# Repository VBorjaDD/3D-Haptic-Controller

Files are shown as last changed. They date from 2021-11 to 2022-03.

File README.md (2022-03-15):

# 3D Haptic Controller
Based on the semester project outcome of Louis Jouret (September 2021- January 2022). Supervisor Victor Borja
Detailed information can be found in [FlyingCelluloReport.pdf](/FlyingCelluloReport.pdf)

## Abstract
This project aims to study the feasibility of haptic feedback in a 3D space. There is an increasing demand for such solutions, mainly in rehabilitation since they remove the need for a daily appointment with a therapist and enable the gamification of rehabilitation.
Some solutions already exist but remain very expensive since they are based on 3-axis arms. Nowadays, a lot of progress in the field of aerial robotics has been done and it is time to consider using the principles of flying drones to take over this task.

## Chasis design and flow simulation
The first approach to the solution consist on a graspable device which includes 4 propellers. The device should account for the user safety as well as for the air flow of the chasis. The proposed solution flow simulation is presented bellow.
Flow

## Trajectory control
To provide an adecuate haptic feedback the device needs to be controlled accuratelly, both to provide a good trajectory as well as "Reject disturbances", which in this case would consist on fighthing the weight of the hand, or providing a resistance against the movement as an exercise.

Control

## State of the protype and stabilization test
Bellow it can be found videos of the last stabilizing test:

https://user-images.githubusercontent.com/30259634/156215392-c507a673-42e5-492a-a674-068f0fa65a87.mp4

https://user-images.githubusercontent.com/30259634/156215643-9cf9c3b2-c321-48e0-aff9-d65be72161e4.mp4

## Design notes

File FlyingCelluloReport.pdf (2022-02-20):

## Flying cellulo for rehabilitation

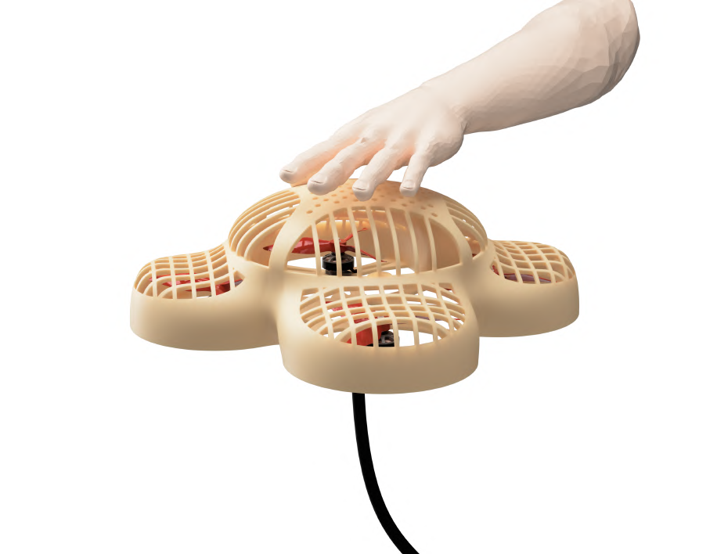
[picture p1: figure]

Louis JOURET - 269882

Professor: Pierre Dillenbourg Advisor: Victor Borja

December 2021

Flying Cellulo for rehabilitation

## Contents

1 Introduction | 1
2 Existing solutions | 1
3 Design | 3
4 Dynamics | 11
5 Control | 12
6 Testing | 17
7 Conclusion | 19

## 1 Introduction

This project aims to study the feasibility of haptic feedback in a 3D space. There is an increasing demand for such solutions, mainly in rehabilitation since they remove the need for a daily appointment with a therapist and enable the gamification of rehabilitation. Some solutions already exist but remain very expensive since they are based on 3-axis arms. Nowadays, a lot of progress in the field of aerial robotics has been done and it is time to consider using the principles of flying drones to take over this task.
The second goal of the project is to propose a proof of concept. Thus a first design will be drawn which will serve us to analyze the technical challenges that have to be overcome to make it a viable solution for rehabilitation. Among these challenges, we count the diculty to draw a graspable drone that remains completely safe and the writing of a control algorithm that is fast enough to create a user-friendly experience.
This work will, first of all, see what has already been done in the field of machine-assisted rehabilitation. Second of all, we will design a first concept that fulfills all the mechanical requirements. Once the design has been done, the dynamics of the model are studied to finally write two dierent control algorithms. The technical work ends with tests of the first material purchased and the first test of haptic feedback. Finally, we will discuss if a flying rehabilitation drone is a feasible solution.
Below is the Gantt chart initially defined at the start of the semester:

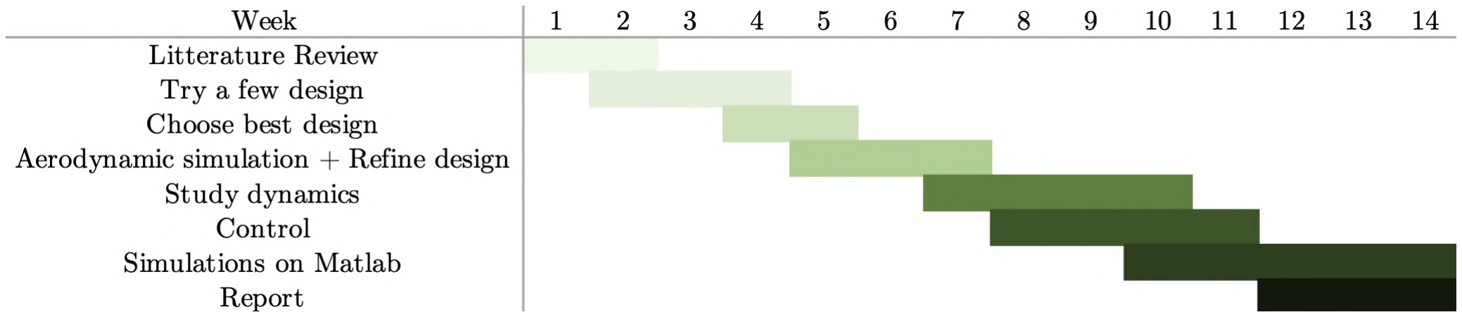
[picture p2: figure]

## 2 Existing solutions

There already exist solutions that are designed for rehabilitation. They are mainly based on a robotic arm that creates haptic feedback to the patient’s hand. One of the most famous products is MIT-Manus. The patient puts his elbow in a support which is held by a robotic arm. The patient then performs dierent movements which are corresponding to divers exercises shown on the screen attached to the robotic arm.

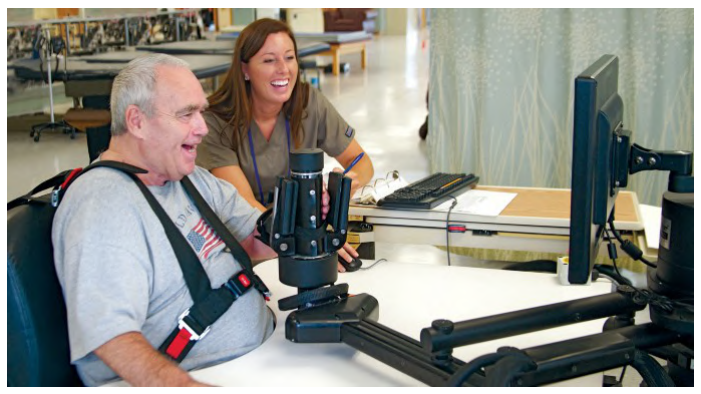
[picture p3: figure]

Figure 1: MIT-Manus [1], Credit: H. I. Krebs, Newman Lab, MIT

Hocoma, which is one of the world leader in advanced technologies for movement rehabilitation, has a complete range of 3 products called Armeo®, designed for the rehabilitation of the arm depending on the severity of the handicap.

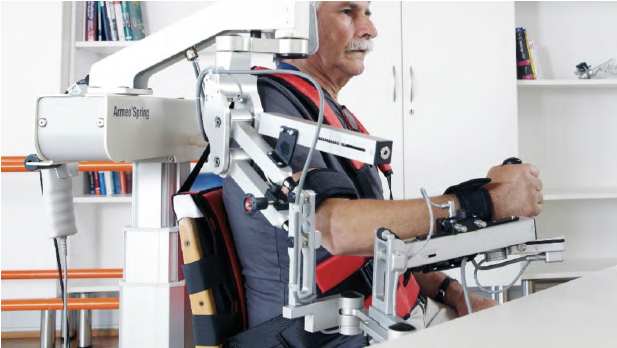
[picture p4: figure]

(a) Armeo®Power | (b) Armeo®Spring

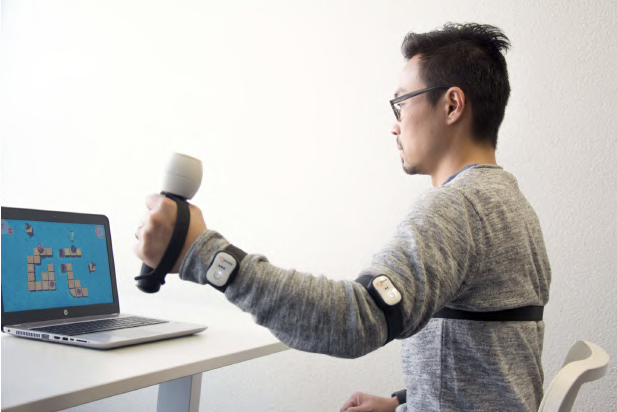
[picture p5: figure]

(c) Armeo®Senso
Armeo®Power [2] is the most powerful solution and can assist and guide the patient’s hand in its movements. Armeo®Spring [3] is a lighter product designed to support the arm’s weight and is thus less powerful. These products come with their monitor on which the patient follows instructions. Armeo®Senso [4]is the lightest product designed for people that can already support the weight of their own arm.
So if a patient needs a product that can create haptic feedback and support the arms weight, the only solutions available are very expensive and impossible to bring home. Thus a flying Cellulo which is capable of supporting the patient’s arm and giving haptic feedback would add value to the market if it can achieve these goals.

## 3 Design

First of all, the power of the Cellulo has to be determined. Since the product needs to assist the patient’s hand and that it should also be able to create resistance, the weight of an adult’s hand is taken as a reference load. Thus the drone should be able to lift the hand without the patient’s help. A simple weighting of 3 dierent hands in dierent positions, gives a maximum weight of 1.5 kg.
Secondly, the fingers have to be protected from the blades. The hand must either be far away from any moving part or the latter have to be covered by a protective grid.
The project is also considering controlling the final product with common video game consoles such as Wii, PlayStation or XBox. Therefore it is necessary to work with a communication protocol that is supported by these platforms. Bluetooth happens to be compatible with the three of them.
Finally, the patient must be able to use the product over a whole workout session, which is not possible with the current battery technology. Hence, the drone has to be supplied with power from the ground. This is not a limiting factor for the user-friendliness of the product since it does not need to fly far away from the ground station.
Thus, the basic requirements that have to be respected whatever the design of the product, are the following:
1. thrust of up to 1.5 kg + own weight
2. safety from the blades
3. Bluetooth as communication protocol
4. no battery on-board

### 3.1 Feasible architectures

There are a lot of very dierent architectures possible to make a drone fly. However, each comes with its perks and drawbacks. Let’s take a closer look at the ones that would be capable of achieving the desired goal:

### 3.1.1 Quadcopter

Figure 3: motor layout of a quadcopter

The quadcopter uses 4 motors which are equidistant to the drone’s center. It is the most seen and popular architecture due to its stability and controllability. Due to its 4 motors, it is the most powerful of the following solutions. However, this comes with high power consumption. But since we are supplied from the ground and are thus not limited by power consumption. The biggest disadvantage of the quadcopter is its footprint. Due to the four propeller, it is not possible to create a compact solution.

### 3.1.2 Tricopter

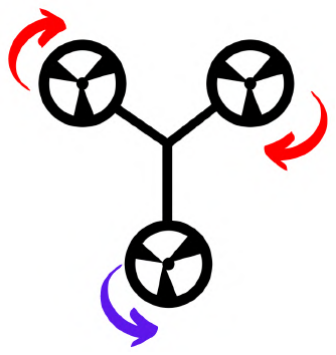
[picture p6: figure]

Figure 4: motor layout of a tricopter

The tricopter can counter the quadcopter’s footprint problem. Only using three propellers makes it compacter and lighter. However, this has its toll on the thrust and the torque applied to the center of mass. Hence, it is less controllable than the quadcopter. Furthermore, the tricopter suers from an asymmetric yaw momentum. Since we don’t have an even number of motors, the motor that spins counterclockwise has to either have a bigger propeller or spin faster than the two clockwise propellers.

### 3.1.3 Bicopter

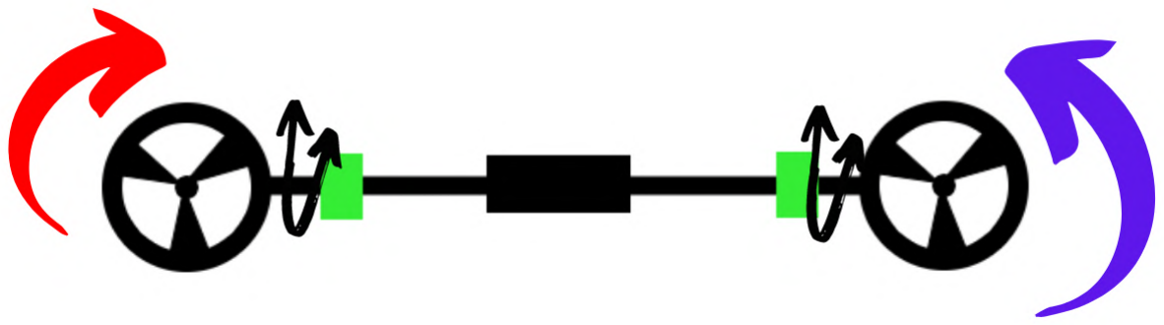
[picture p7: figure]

Figure 5: motor and servo (green) layout of a bicopter

The bicopter configuration is an even more extreme architecture in which only two motors are used. This reduces the footprint even more and thus allows the most compact solution. However since two motors in a plane lack a degree of freedom to be able to be used in our project, two servos have to be added to the structure to incline the motors. In Figure 5 the servos are represented in green.
In addition, the bicopter is heavily limited by its thrust since only two motors have to deliver the whole force. Since the project requires lifting a payload of 1.5 kg, this comes as a big downside.

### 3.1.4 Final choice

Due to the nature of the project, the drone will have to lift heavy payloads but remain compact. Unfortunately, the only solution that would be able to lift a payload of 1.5 kg without taking a hit on its controllability is the quadcopter. Thus it is the architecture that was chosen for the realization of this project. Before designing the 3D model, the propeller size has to be chosen since it will impact the design significantly. After consulting various datasheets, we settle for 5 inches. It is a good compromise between size and thrust. Generally, the bigger the size, the more thrust we get for a given power. Furthermore, we can already decide which onboard computer we will use. The Raspberry Pi has a Bluetooth module and great documentation. Unfortunately, it is quite heavy. Thus we purchased the all-new Raspberry Pi Zero 2W which has all the communication features we need but weighting 5 times less.

### 3.2 Design iterations for the 3D model

Once the system’s architecture has been chosen, the first 3D model can be created. The models have to respect the safety of the patient and let enough airflow through the chassis. Limiting the air obstruction is primordial to guarantee sucient thrust and stability. Thus the first 3D model that satisfies all the design requirements will go through a fluid dynamics simulation to test its aerodynamic eciency. If the simulation shows some flaws in the design, the latter is changed and the simulation is rerun. This iteration is done until the simulations deliver satisfactory results. This design is then taken on a real testbench, where the thrust is measured, with and without the chassis, to check if the chassis is not obstructing the airflow too much.

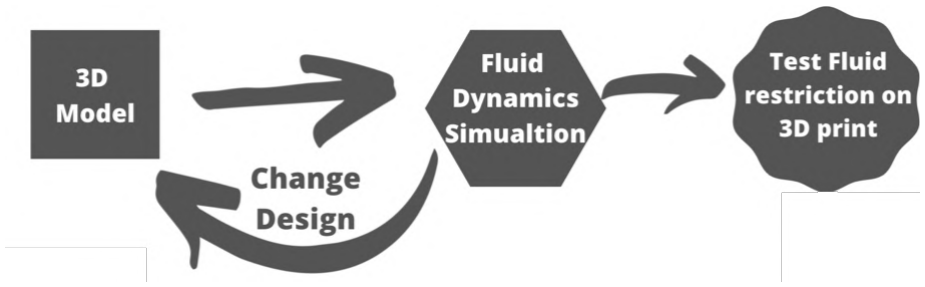
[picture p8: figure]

Figure 6: design plan for the chassis

### 3.3 Fluid Simulations

The software used to perform the simulations is Ansys Discovery Live. This software is very simple to use and is sucient in our case. The 3D models that are tested are simplified versions of the final model that do not have protection grids/nets and do not have motor mounts. This saves valuable time and is not necessary to compare dierent designs since the air resistance of the grid/net will remain quite constant through all the designs.

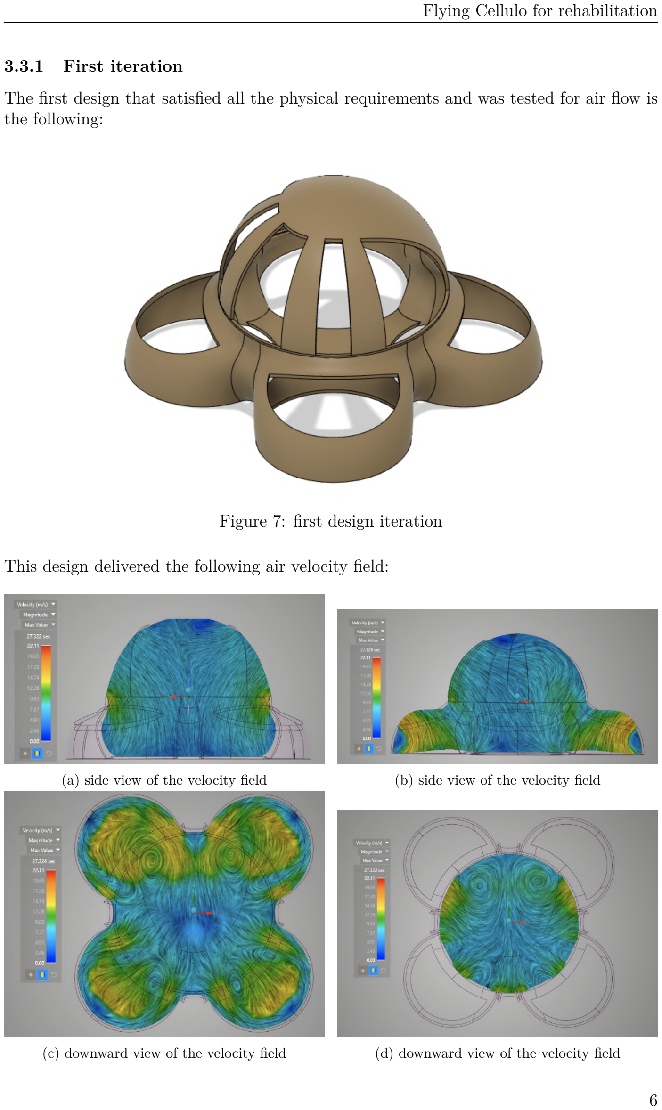
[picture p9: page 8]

### 3.3.1 First iteration

The first design that satisfied all the physical requirements and was tested for air flow is the following:

Figure 7: first design iteration

This design delivered the following air velocity field:

(a) side view of the velocity field | (b) side view of the velocity field
(c) downward view of the velocity field | (d) downward view of the velocity field

As can be seen in (a) the airstream has to corner around the upper opening and thus creates a faster stream closer to the rotation point. This could be resolved by reducing the angle of air intake. (b) shows that the airflow coming from the upper part of the chassis is small compared to the flow coming directly from the fan pockets. To balance the two contributions, we should increase the size of the upper pockets and bring them closer to the fans. (c) and (d) are showing a lot of turbulence inside the core. To avoid those, the lower part of the hand support should get slimmer.

### 3.3.2 Last iteration

After 4 dierent iteration and simulations of dierent design parameters we settled for the following:

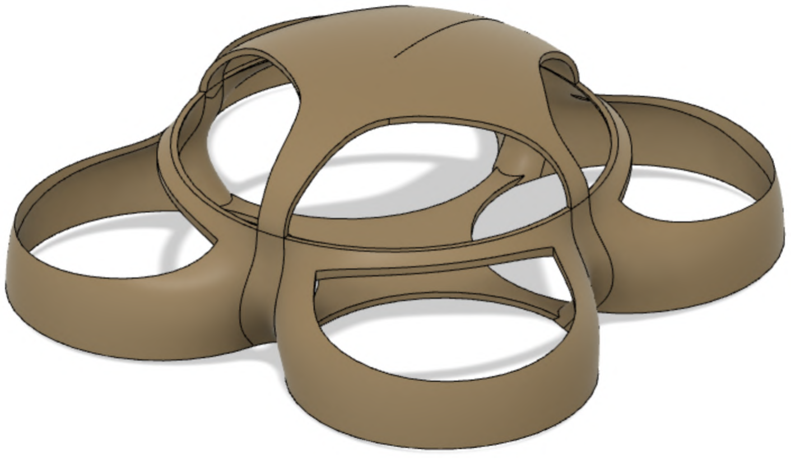
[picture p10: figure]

Figure 9: last design iteration

The upper pockets got widened and lowered to increase the airflow coming from the upper part of the chassis. Since the upper pockets are now directed downwards, the airstream does no longer need to corner. Furthermore, the fan pockets got bigger to increase the airflow coming directly from above the fan. These two major changes allow us to get a much smoother/even velocity profile and less turbulence compared to the first iteration.

(a) isometric view of the velocity field | (b) side view of the velocity field

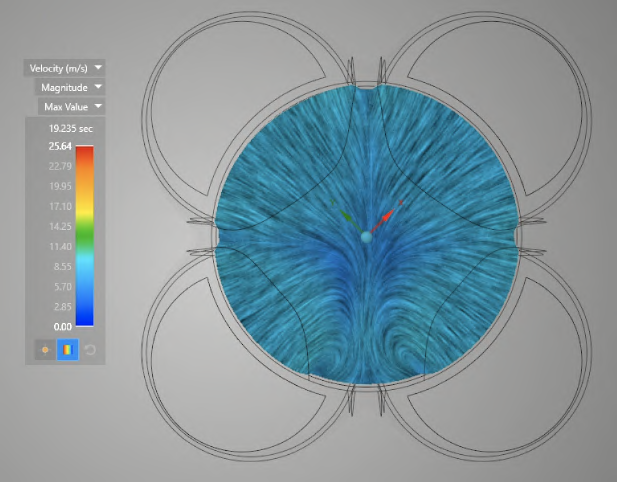
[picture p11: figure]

(c) downward view of the velocity field | (d) downward view of the velocity field

### 3.4 Finalization of the 3D model

Now that the main shapes of the design are validated, the final part of the 3D design consists of adding safety grids/nets and the motor mounts. The choice between grids or nets can at this stage not be determined since the drone is not flying yet and the impact on user-friendliness can not be determined. This will have to be tested once the drone is used and both solutions can be tested. Thus, grids will be used for the finalization of the design but can always be replaced later by nets. Concerning the propellers, the only parameter that can be changed is the number of blades and the pitch. The theory says that the more blades a propeller has, the more thrust it can produce but the less controllable it is. The optimal number of blades will have to be determined through empirical testing, once the drone is flying. For the moment we settled for 3 blades. The final design including safety grids, motor mounts, propellers, a Raspberry Pi and a whole for the supply cable looks like this:

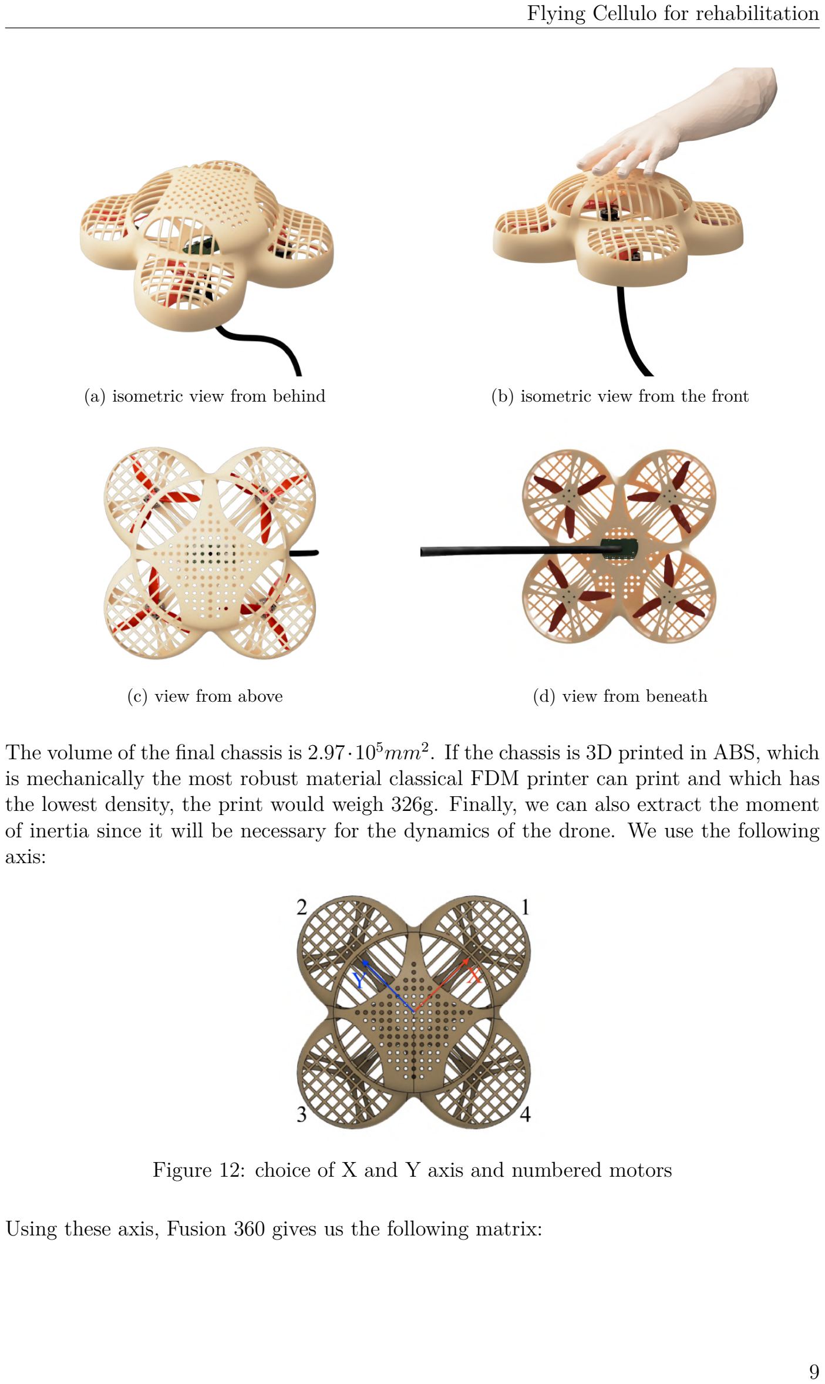
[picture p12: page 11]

(a) isometric view from behind | (b) isometric view from the front
(c) view from above | (d) view from beneath
The volume of the final chassis is 2.97·10⁵mm2. If the chassis is 3D printed in ABS, which is mechanically the most robust material classical FDM printer can print and which has the lowest density, the print would weigh 326g. Finally, we can also extract the moment of inertia since it will be necessary for the dynamics of the drone. We use the following axis:

Figure 12: choice of X and Y axis and numbered motors

Using these axis, Fusion 360 gives us the following matrix:

I =

S
W
W
U
I11 =2.66 | I12 = ≠3.53 · 10≠2 I13 =2.51 · 10≠2
I21 = ≠3.53 · 10≠2 I22 =2.66 | I23 =2.43 · 10≠2
I31 =2.51 · 10≠2 | I32 =2.43 · 10≠2 | I33 =4.64

T
X
X

V · 10≠3

[kgm2
] (1)

To greatly simplify the dynamics equations we can approximate the small moment of inertia by zero. This is the matrix that will be used:

I =

S
W
W
U
2.66 0 | 0
0 | 2.66 0
0 | 0 | 4.64

T
X
X

V · 10≠3

[kgm2
] | (2)

### 3.5 Cost

After having designed the chassis and knowing its volume we can finally do a cost estimation for the first prototype. This cost estimation does not take into account the power supply on the ground since the price can fluctuate a lot depending on quality.
Motor: 4x F40PRO IV KV1950 (24V) from T-motor 4 x 27 CHF
Speed controller: F55A PRO II F3 6S 4IN1 from T-motor 104 CHF
Propellers : 4x T5150 from T-motor 4 x 0.7 CHF
Rasberry Pi 50 CHF
326g of ABS 18CHF/kg x 0.326kg
2x 2.5m cable of 6mm2 2 x 2.5m x 1.8 CHF/m
Total 280 CHF

Adding to this a power supply, which costs at least 100 CHF for correct quality, brings the whole project to a pretty high price tag. The majority of the price comes from the motors and their controller which are very powerful. If after the first tests, the level of power initially estimated seems to be unnecessary, a smaller controller and motors can be mounted instead which will drastically drop the price.

## 4 Dynamics

In this section, we will derive the dynamics of the drone. [5] helped at this task. We chose a 12-state description for the cellulo:

x =[–, —, “, –˙ , —˙, “˙ , x, y, z, x,˙ y,˙ z˙] | (3)
We will write p =[x, y, z] as the position and ◊ =[–, —, “] the roll, pitch and yaw. The input are the four motor thrusts u =[u1,u2,u3,u4].
Each motor produces a force and a torque proportional to its thurst:

Fi = kF ui
Mi = kMui
The total force and torque can be expressed as follows:
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
kF | kF | kF | kF
0 | kF a | 0 ≠kF a
≠kF a | 0 kF a | 0
kM | ≠kM | kM | ≠kM

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
The angular dynamics of the system are given by:

¨◊ = I≠1

(≠ ˙

◊ ◊ I ˙
| ◊ +

S
W
W
U
| | M– M— M“

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
| | | MXext MY ext MZext

T
X
X
V) (5)

p¨ = 1
m

F˛ = ≠˛g +

F
m˛zc + F˛

ext =

S
W
W
U

F

msin(—)+ FXext
≠F

mcos(—)sin(–)+ FY ext
≠g + F

mcos(–)cos(—)+ FZext

T
X
X

V (6)

where F˛

ext and M˛

ext are the external force and torque applied by the patient. Using equation (4), (3), (5) and (6) we can now express the state-space of the system:

x˙ = f(x,u)=

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
1 (x6x5(I2 ≠ I3)+ kF a(u2 ≠ u4)+ MXext I≠1
2 (x4x6(I3 ≠ I1)+ kF a(u3 ≠ u1)+ MY ext I≠1
3 (x4x5(I1 ≠ I2)+ kM(u1 ≠ u2 + u3 ≠ u4)+ MZext x10
x11
x12
kF

m (u1 + u2 + u3 + u4)sin(x2)+ FXext
m
≠kF

m (u1 + u2 + u3 + u4)cos(x2)sin(x1)+ FY ext
m

### ≠g + kF

m (u1 + u2 + u3 + u4)cos(x1)cos(x2)+ FZext
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
## 5 Control

Now that all the dynamical equations have been derived, control algorithms can be written and compared. We will analyze two algorithms which dier a lot in the sense that one will be able to predict the patient’s movements and thus better prepare for it and another one will just react to the current state but will therefore be a lot less resource-intensive and can thus perform at higher frequencies.
To lighten the control computations we need to linearize (7). The linearization around a nominal point can be expressed using the Taylor expansion:

x˙ = f(x, u)
= fi(¯x, u¯)+ ”fi(¯x, u¯)
”x1

x˜1 + ... +

”fi(¯x, u¯)
”xn

x˜n +

”fi(¯x, u¯)
”u1

u˜1 + ... +

”fi(¯x, u¯)
”un

u˜n + p(x, u)
¥

ˆf
ˆx

x +

ˆf
ˆu

u
= Ax + Bu
Now we can discretise the state-space:

x(k)= Ax(k)+ Bu(k)
≈∆

x(k + 1) ≠ x(k)
h | = Ax(k)+ Bu(k)
≈∆ x(k + 1) = (hA + I)x(k)+ hBu(k) ≈∆ x(k + 1) = x(k)+ u(k)

### 5.1 LQR Control

The first controller is an LQR controller which stands for Linear-Quadratic regulator. This controller is minimizing a cost function composed of a first quadratic term representing the deviation from the reference state and a second quadratic term representing the magnitude of the input:

J = ÿŒ

k=0

xT

k Qxk + uT
k Ruk

where the matrices Q and R have to be tuned by the designer.
The classical LQR optimal input is given by:
uk = ≠Kxk where K =(R + TP)≠1(TP + NT ) and P is the solution of the Riccati equation. Fortunately, MATLAB already has an integrated function that computes K. We could also have used a Proportional-Derivative controller, but unfortunately they are quite dicult to tune for a system with as many states. With the LQR, we directly get the optimal K with respect to Q and R. Since R tunes the cost of input, the higher we set R the more economic the drone will fly. However, we are supplied from the ground and thus do not need to be economic. Hence to get the best reactiveness we set R to zero. Now that R is set to zero, the value of Q doesn’t matter for the solution of the cost function. In the algorithm, Q was set to the identity matrix. In our case, we also need an integrator because otherwise the drone would not come back to its initial position after a hand is put on it. The integrator accumulates all the errors overtime to produce a supplementary input of weight –. Furthermore, we add the nominal input which corresponds to a quarter of the drone’s weight to the input to avoid an initial drop in altitude. Thus our input is given by:

uk = ≠Kxk ≠ –K ÿ

k

i=0

(xk ≠ xref )+ unominal

where – =0.05 rendered satisfactory results.
Using this controller and the dynamical equation, we can now simulate the quadcopter’s behavior when subject to various external forces and torques.
To compare the dierent controllers we will apply the same external forces and torques, which are:

Fext =

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
N | Mext =

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
0.05
≠0.05
0

T
X
X
V

Nm

They should represent the forces applied by a hand of approximately 1.5kg. We add 5N force to the x and y-axis since it is impossible for the patient to apply a perfectly vertical force. Furthermore, the force will be applied as a ramp because the patient will not drop his whole hand instantly. This is the force profile that will be applied:

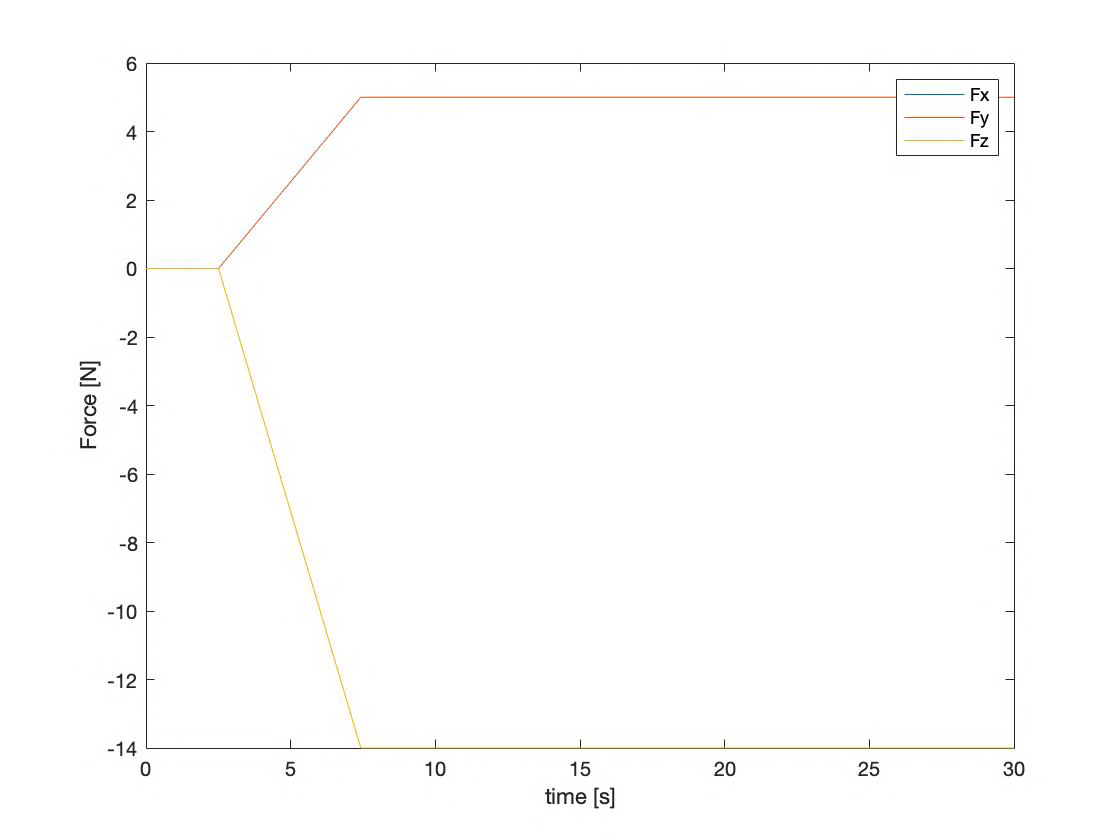
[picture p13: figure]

Figure 13: force profile through time

We apply the same ramp up for the torques.
If these external perturbations are applied to the quadcopter we get the following results:

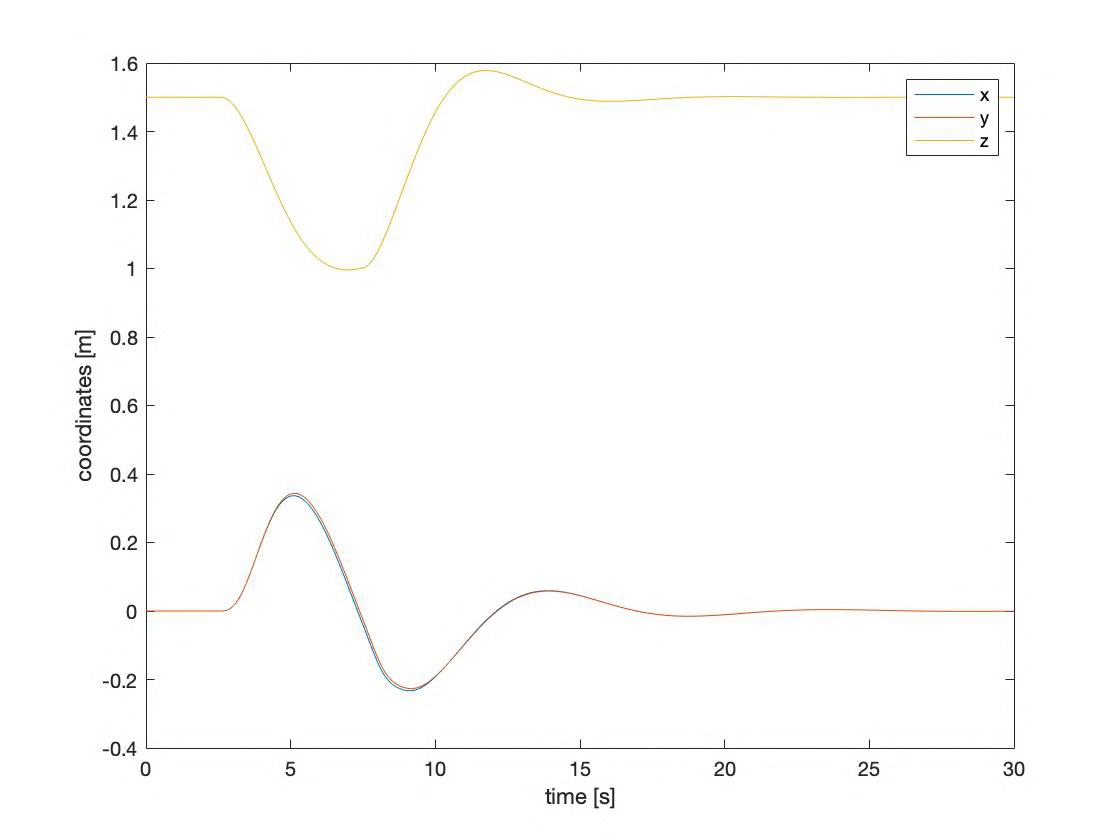
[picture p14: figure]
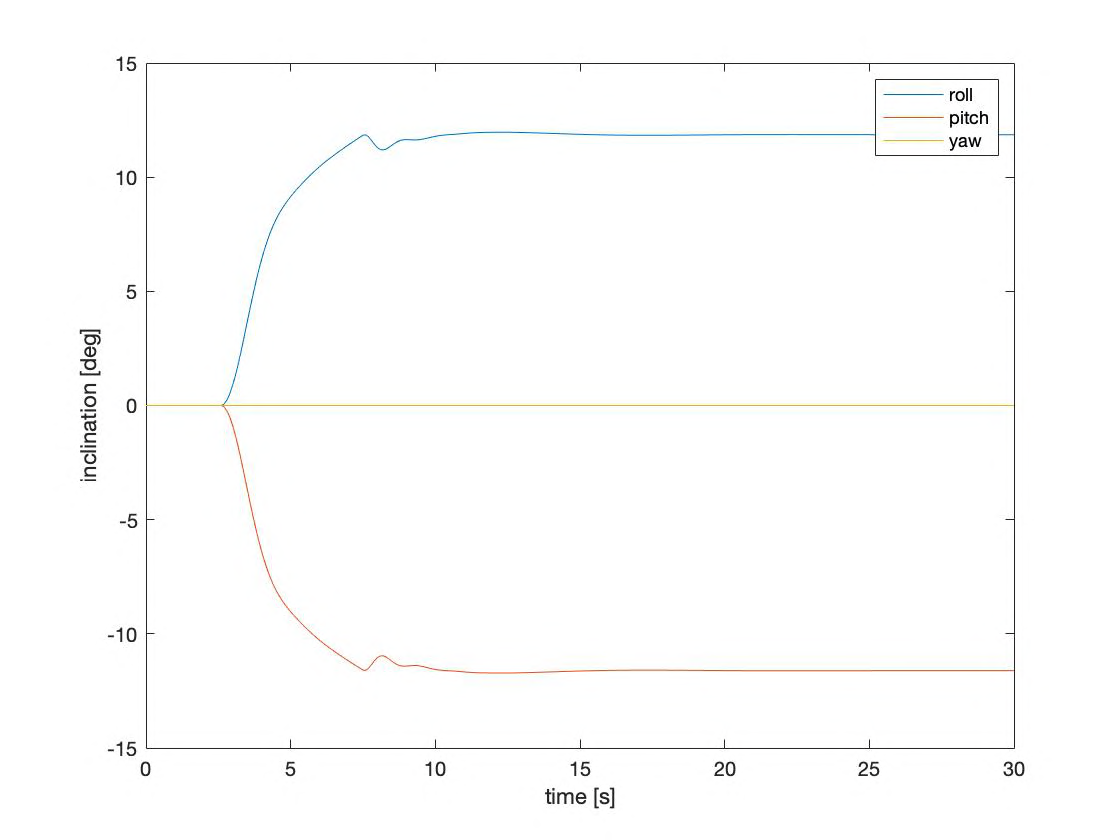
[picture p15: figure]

(a) coordinates of the drone through time | (b) inclination of the drone through time

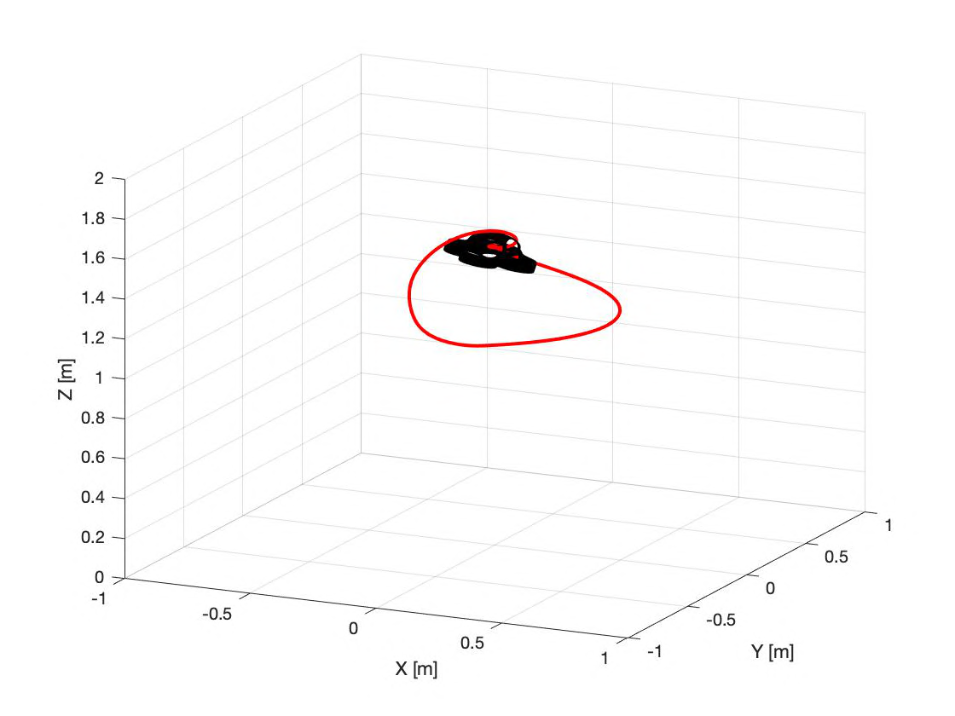
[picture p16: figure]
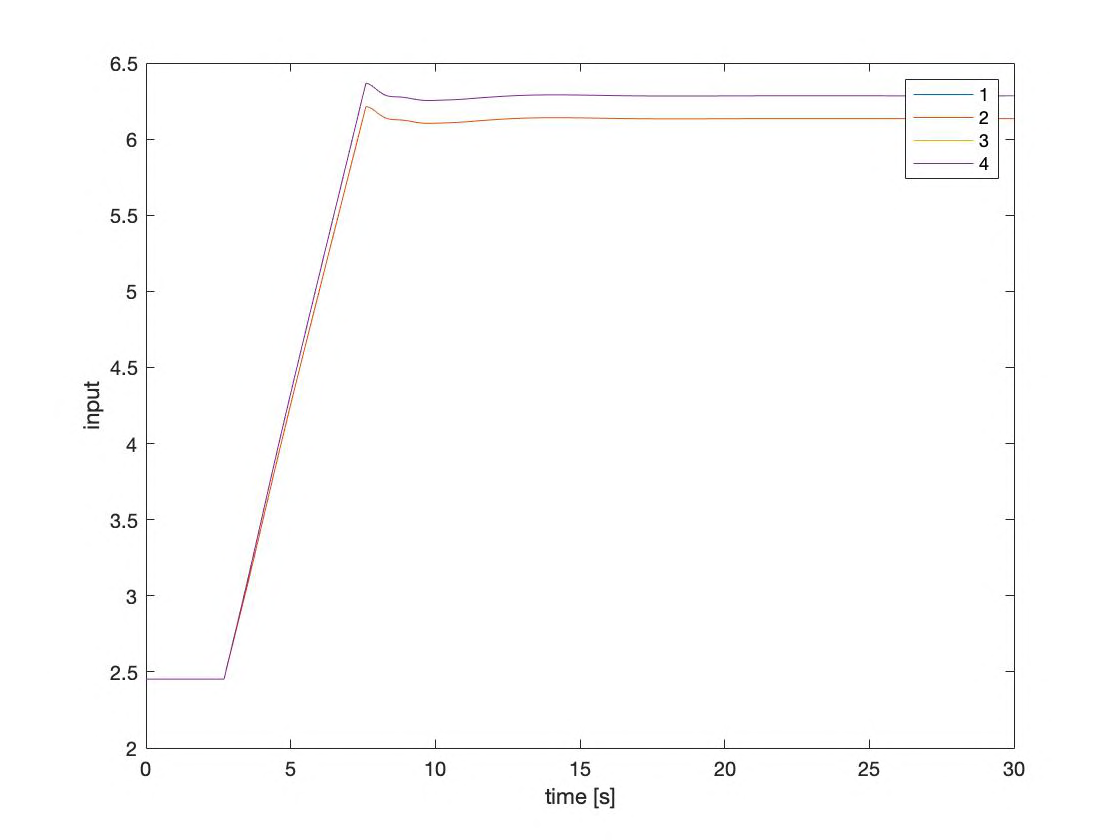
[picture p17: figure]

(c) trajectory of the drone | (d) amplitude of input for each motor
As can be seen in the figures above, the drone manages to stabilize after the disturbances have been applied. However, the drone suers from a few problematic behaviors. Firstly we can observe a huge drop in altitude (0.5m drop) when the hand is placed on it. Secondly, due to the small forward force of 5N we applied to the drone, the drone moves too much forward (0.4m). This misbehavior is due to the fact that the controller does not know when the patient will put his hand on it and thus cannot predict to increase the thrust beforehand. This could be resolved by a Model Predictive Controller.

### 5.2 Model Predictive Control

MPC is an optimal control computed over a finite horizon. The advantage of MPC is first of all that we can add as many constraints to our problem as we want. Furthermore, it will be able to foresee the wanted trajectory and thus better behave. However, the drawback is that this controller needs substantially more computational power.
The framework used to write the algorithm on MATLAB is CasADi. CasADi is an opensource tool for nonlinear optimization and algorithmic dierentiation. [6] has been very helpful to write clear code with CasADi.

The MPC optimization problem can be expressed as follows:

min

˛u

N

ÿ≠1

k=0

˛xT

k Q˛xk + ˛uT
k R˛uk
s.t. ˛x0 = ˛x0 ≠ ˛xref
˛xk+1 = ˛xk + ˛uk

(8)

After all the inputs have been optimized for the next N steps, only u0 is fed to the system. In our case, to take advantage of the predictive capacity of MPC, we will feed the force profile into the state-space so that the controller can foresee and counteract the patient’s touch. Simulating the drone with the same external disturbances as seen in the LQR controller we get the following results:

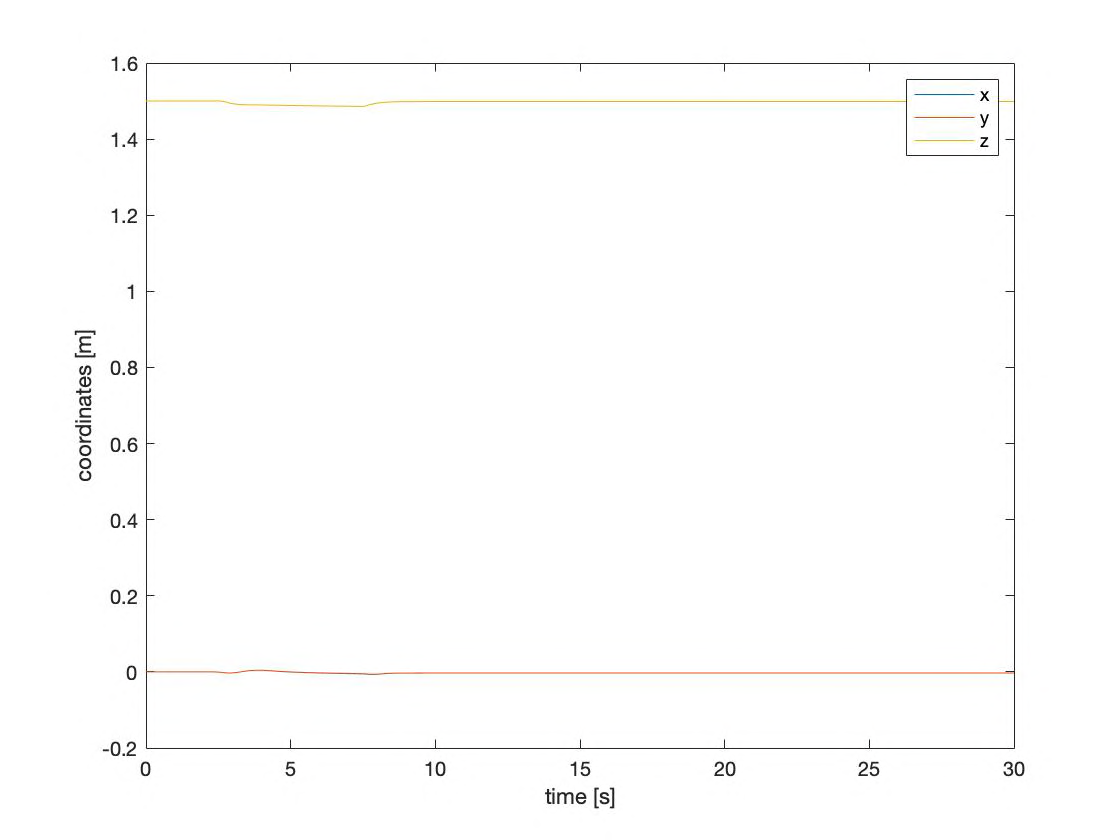
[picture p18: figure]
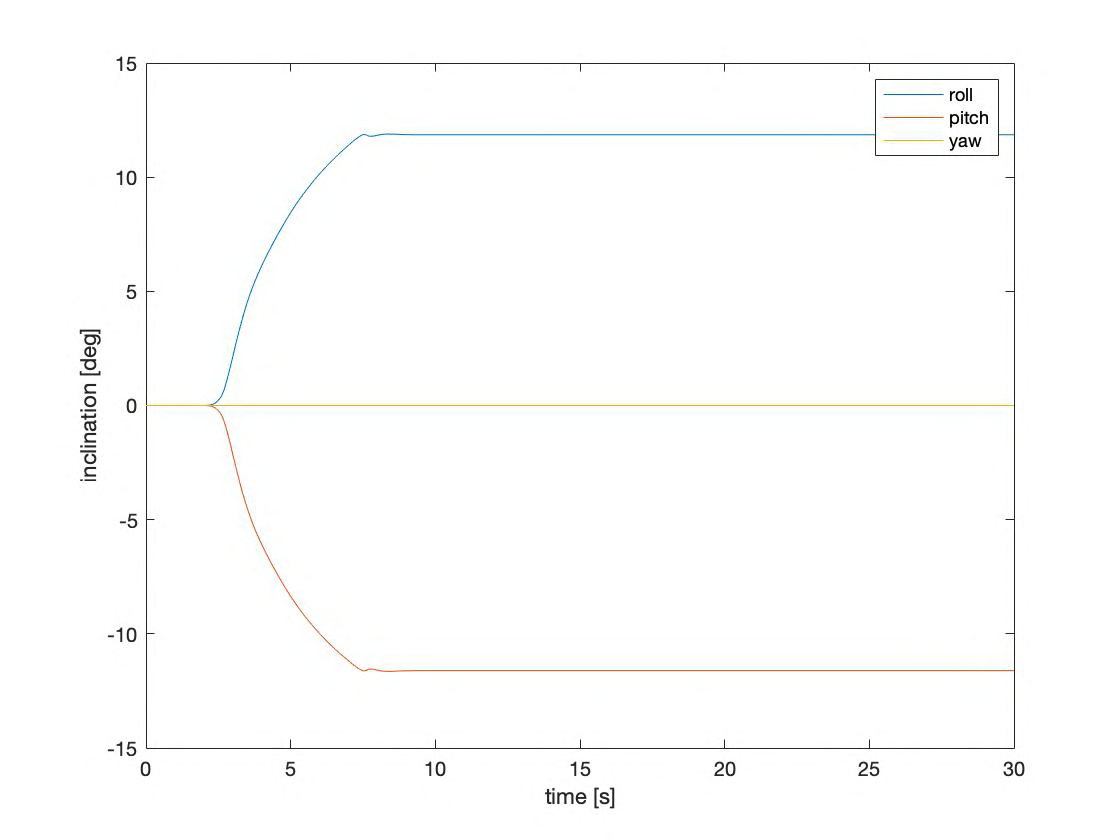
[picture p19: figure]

(a) coordinates of the drone through time | (b) inclination of the drone through time

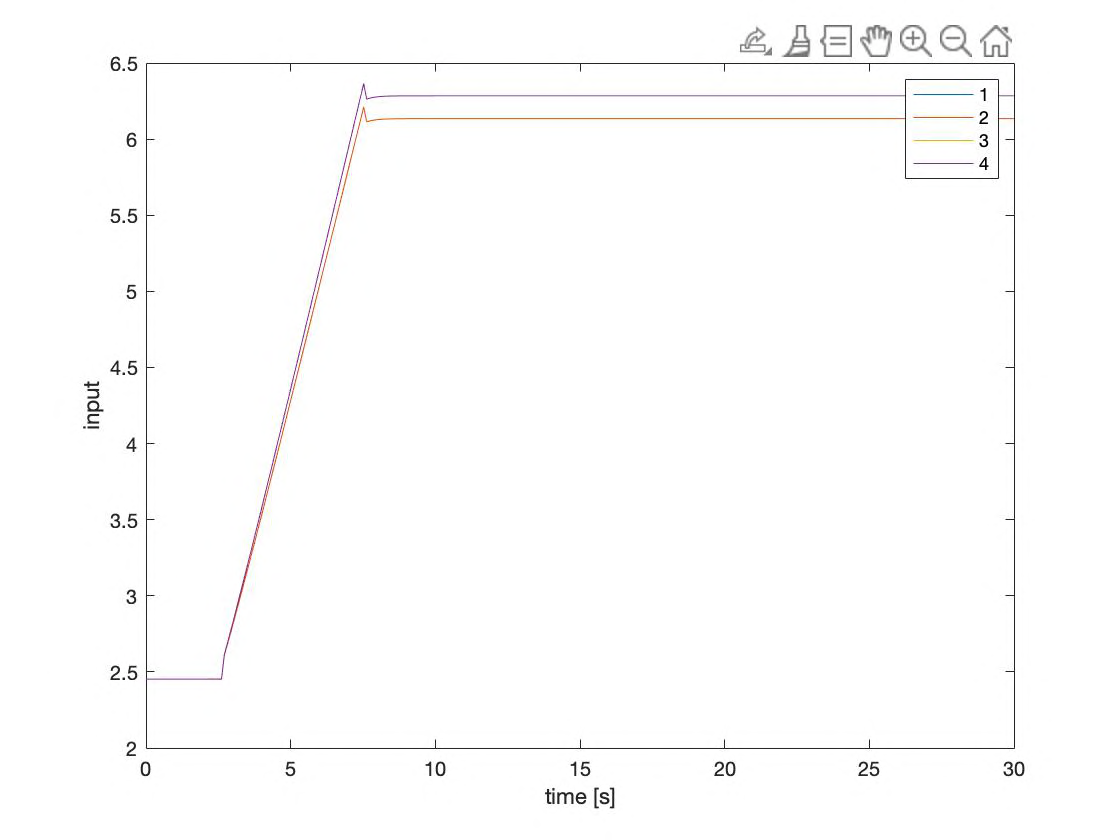
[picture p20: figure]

(c) trajectory of the drone | (d) amplitude of input for each motor
As can be seen in the plots above, the controller perfectly counteracts the forces and torques. At first glance, it looks like the computed inputs look perfectly identical to the LQR’s. However, if we plot both on the same graph and zoom in on the moment the hand touches the drone, we realize that the MPC controller is doing a jump in intensity before the ramp. This shows that it could predict the hand’s weight and increases the throttle before it is too late.

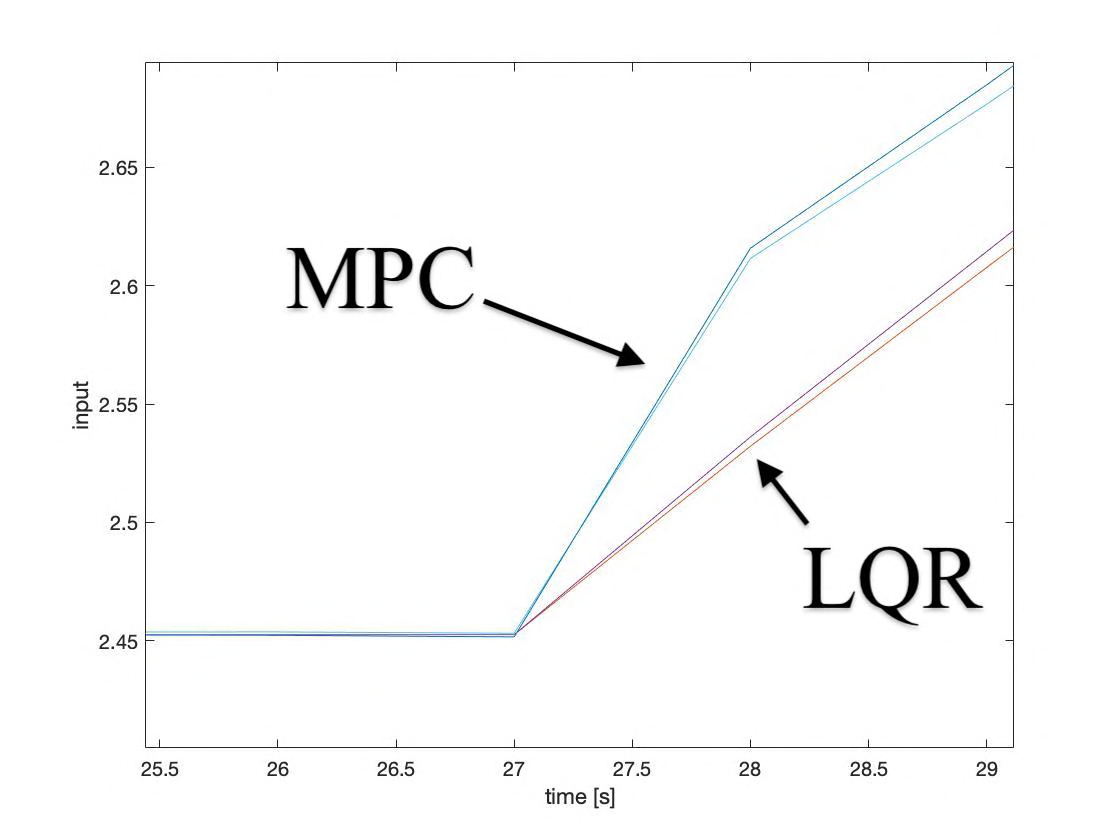
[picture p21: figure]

Figure 16: dierence in input intensity between MPC and LQR

Unfortunately, MPC is a very resource-intensive controller and thus needs a lot of computational power. If this controller,as it stands, is able to run on a Raspberry Pi Zero 2W is currently unknown but unlikely. However, there are some parameters that can be tuned like N the number of iterations per optimization and the time horizon which determine how far into the future the controller is seeing. A smaller time horizon would make the controller much lighter in computation but still a heavy task for a Raspberry Pi Zero. Furthermore, future work will have to be done on the prediction of the moment of touch. This can be done using proximity sensors or cameras for example. The complexity of this additional work is another drawback for MPC. However, the performance dierence between LQR and MPC are huge and thus continuing to inspect this solution seems important.

## 6 Testing

### 6.1 Relationship between Thrust and Duty Cycle

Now that the controllers have been defined, it is time to test the motors and find the relationship between the input and the actual thrust. Since the motors that are used for such applications are brushless DC motors, the command will be given in duty cycles. To measure the thrust of a motor we fix the motor on a load cell, which emits a voltage proportional to its bending.

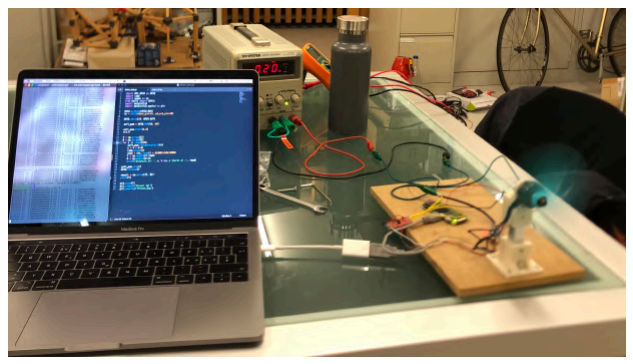
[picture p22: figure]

(a) bending of the load cell through thrust | (b) picture of the setup
The components used for the build of this testbench are:
Motor: F40PRO IV KV1950 from T-motors : 27 CHF
Controller: F45A from T-motors : 29 CHF
Load cell: SEN-13329-TAL220 from SparkFun Electronics 10 CHF
Load cell amplifier: SEN-13879-HX711 from SparkFun Electronics 12 CHF
Thus, we can increase the duty cycle, read o the power drawn from the power supply, measure the thrust and represent it in the following graph:

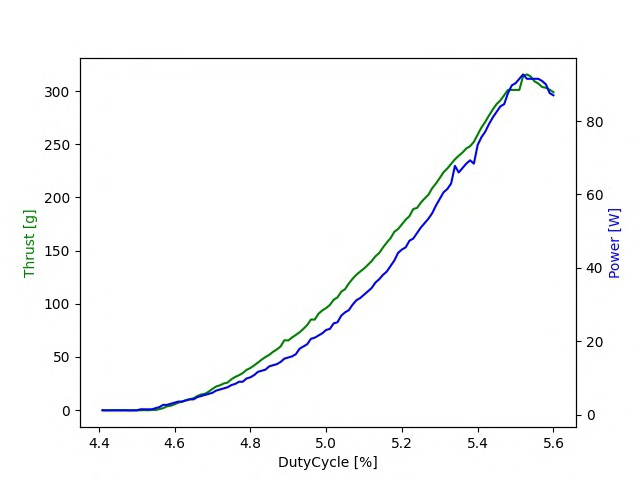
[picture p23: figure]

Figure 18: Thrust and power in function of duty cycle

Unfortunately, the power supply of the CHILI Lab is limited to 90W and thus we could not test the complete range of power. Nevertheless, this graph gives valuable information about the relationship between the duty cycle and the thrust. After plotting some functions on top of this graph we found that a good function that approximates the relationship is the following:

T hrust = 255 · (DC ≠ 4.4)²
≈∆ DC =

Û
T hrust
255 +4.4

This relationship is valid for a thrust under 300g and will have to be validated for a higher thrust once a bigger power source is found. This function enables us to find the proper DC command once the control algorithm has computed the thrust needed to stabilize the quadcopter.

### 6.2 Inclination control

In the last week of the project, we decided to build a small testbench to test the controller on the inclination. Namely, to fix the position of the drone in space and to let it rotate on a ball joint. Unfortunately, we had some issues with the delivery of the parts and the whole test fell through. If the project is taken over, this would be an interesting point to start with since it greatly simplifies the testing of the controller by only focusing on the inclination. Thereby, the controller would be able to perfectly stabilize before starting to control the space coordinates.

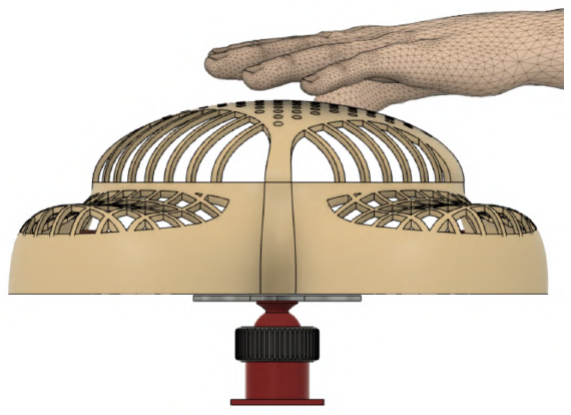
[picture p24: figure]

Figure 19: Cellulo attached to a ball joint

## 7 Conclusion

In this project we did the initial research to analyze the feasibility of a flying drone as a rehabilitation solution. However, a lot of work still has to be done to confirm if the product is really commercially viable since user-friendliness is impossible to measure at this point of development.
The biggest advantage of our solution compared to a 3-axis arm is price. Furthermore, it is a much more compact product that can be brought home without a problem. Nevertheless, this comes with much lower force feedback. A second drawback is a high sound and air blow that will come from the drone compared to the arm. The latter will have to be accessed once the drone is flying.
Regarding the 3D design, it will have to be checked for safety once the drone is up and flying. Even if it is an extremely important requirement, it seems to be the most accessible. If some flaws in the safety are detected by future developers after putting the drone in the air, the rectification should not be that challenging. As for the manufacturing of the chassis, it will have to be 3D printed for the duration of development which will come as an additional challenge considering that most common 3D printers do not support this size.
Concerning the controller, we showed that the MPC can successfully reject the external disturbances coming from the patient’s hand. The next challenge would be first of all trying to run the controller on an on-board computer such as the Raspberry Pi 2W and secondly design a way to predict the moment of the patient’s touch. This could for example be done using proximity sensors on the drone. In addition, the force profile of a typical touch should be studied to best predict the input needed.
As for the testing, it is unfortunate that we did not get our hands on a more powerful power source to test the total range of duty cycles. A test was scheduled and performed with the «Laboratoire des systèmes électriques distribués» but was unsuccessful due to a mechanical flaw (play in the propeller). Future developers will have to either purchase a more powerful power supply or recontact another lab.
Regarding the cost of the drone, we could reduce the price by using motors and a controller that are less powerful. The price given in this report of 280CHF was for the prototype which is quite certainly over-dimensioned to be able to validate the first proof of concept. Once the first prototype has been built, the size of the motors will be reduced depending on the performance of the prototype and the personal opinion on the user-friendliness of the developers. All in all, we estimate the final production costs at 50% of the prototype’s cost.
All the initial goals of the Gantt chart were achieved, and additional challenges were introduced, however, not all of them were fulfilled due to time constraints. Future developers can start with the building of a testbench, demonstrating the working of the controller on the rotation of the Cellulo. All the files and codes can be found in the project’s GitHub repository: https://github.com/VBorjaDD/FlyingCellulo
Special thanks to Victor Borja who supervised this project.

## References

[1] M. Costandi, “Rehabilitation: Machine recovery,” Nature.
[2] “Armeo®power.” https://www.hocoma.com/solutions/armeo-power/.
[3] “Armeo®spring.” https://www.hocoma.com/solutions/armeo-spring/.
[4] “Armeo®senso.” https://www.hocoma.com/solutions/armeo-senso/.
[5] P. Wang, “Dynamics modelling and linear control of quadcopter,” IEEE.
[6] “Casadi documentation.” https://web.casadi.org/docs/.

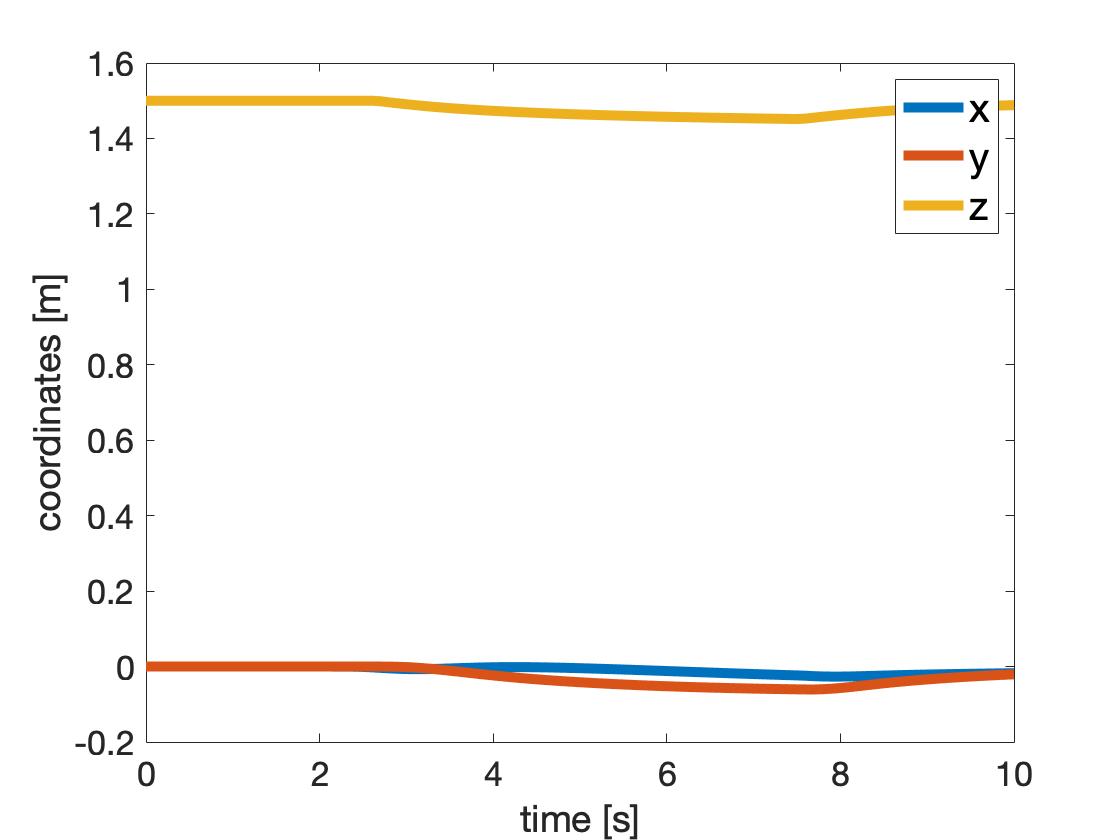
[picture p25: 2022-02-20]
MATLAB/mpc.jpg

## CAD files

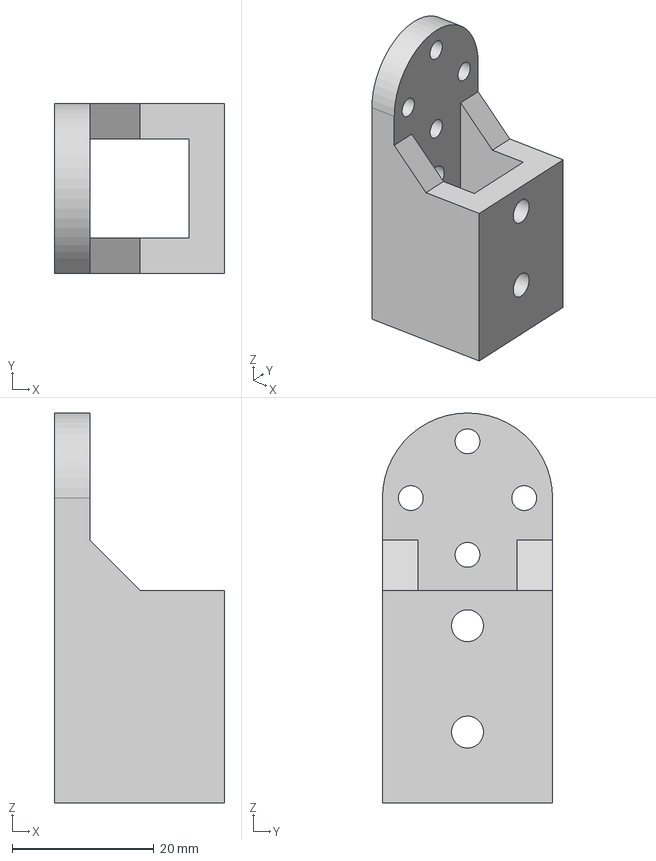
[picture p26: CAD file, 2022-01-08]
CAD/Motorbench/Motorbench Top.step
24.0 x 24.0 x 55.0 mm

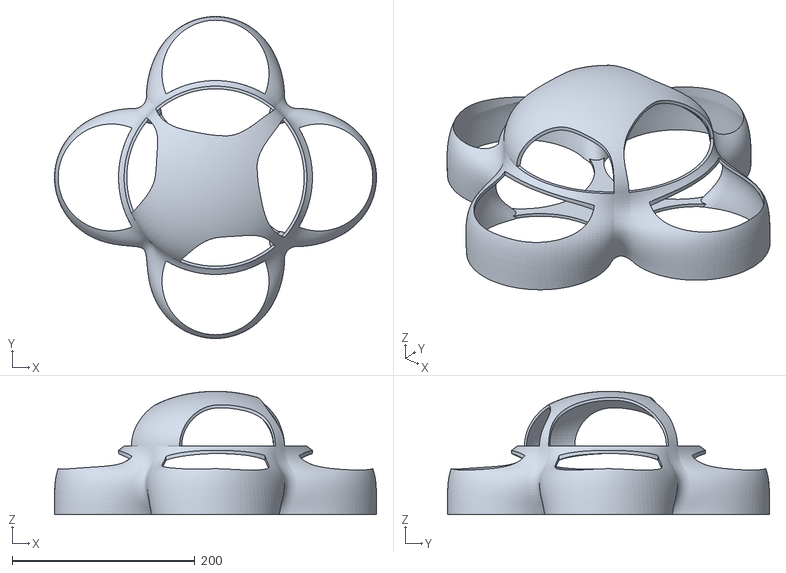
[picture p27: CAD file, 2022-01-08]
MATLAB/Cellulo.stl
352.3 x 352.3 x 135.0

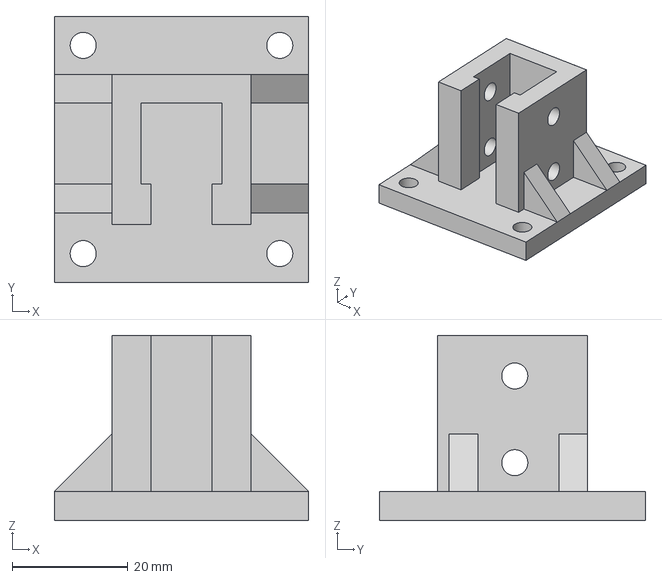
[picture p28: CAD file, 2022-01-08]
CAD/Motorbench/Motorbench socle.step
44.0 x 46.0 x 32.0 mm

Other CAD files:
CAD/Motorbench/Motorbench Top.stl
CAD/Motorbench/Motorbench socle.stl

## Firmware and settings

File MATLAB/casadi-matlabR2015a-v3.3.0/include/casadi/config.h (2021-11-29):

/*
 *    This file is part of CasADi.
 *
 *    CasADi -- A symbolic framework for dynamic optimization.
 *    Copyright (C) 2010-2014 Joel Andersson, Joris Gillis, Moritz Diehl,
 *                            K.U. Leuven. All rights reserved.
 *    Copyright (C) 2011-2014 Greg Horn
 *
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
 */
#ifndef CASADI_CONFIG_H // NOLINT(build/header_guard)
#define CASADI_CONFIG_H // NOLINT(build/header_guard)

#define CASADI_MAJOR_VERSION 3
#define CASADI_MINOR_VERSION 3
#define CASADI_PATCH_VERSION 0
#define CASADI_IS_RELEASE 1
#define CASADI_VERSION_STRING "3.3.0"
#define CASADI_GIT_REVISION "657a05226363f7d6f57f6c789a208199d75f0fc1"  // NOLINT(whitespace/line_length)
#define CASADI_GIT_DESCRIBE "3.2.0-7.657a052"  // NOLINT(whitespace/line_length)
#define CASADI_FEATURE_LIST ""  // NOLINT(whitespace/line_length)
#define CASADI_BUILD_TYPE "Release"  // NOLINT(whitespace/line_length)
#define CASADI_COMPILER_ID "Clang"  // NOLINT(whitespace/line_length)
#define CASADI_COMPILER "/Applications/Xcode.app/Contents/Developer/Toolchains/XcodeDefault.xctoolchain/usr/bin/clang++"  // NOLINT(whitespace/line_length)
#define CASADI_COMPILER_FLAGS " -std=c++11 -fPIC -fvisibility=hidden -fvisibility-inlines-hidden   "  // NOLINT(whitespace/line_length)
#define CASADI_MODULES "casadi;casadi_linsol_lapacklu;casadi_linsol_lapackqr;casadi_sundials_common;casadi_integrator_cvodes;casadi_integrator_idas;casadi_rootfinder_kinsol;casadi_nlpsol_ipopt;casadi_nlpsol_bonmin;casadi_conic_qpoases;casadi_conic_clp;casadi_linsol_csparse;casadi_linsol_csparsecholesky;casadi_linsol_ma27;casadi_xmlfile_tinyxml;casadi_nlpsol_blocksqp;casadi_conic_hpmpc;casadi_nlpsol_ampl;casadi_conic_nlpsol;casadi_importer_shell;casadi_integrator_rk;casadi_integrator_collocation;casadi_interpolant_linear;casadi_interpolant_bspline;casadi_linsol_symbolicqr;casadi_linsol_qr;casadi_linsol_ldl;casadi_linsol_lsqr;casadi_nlpsol_sqpmethod;casadi_nlpsol_scpgen;casadi_rootfinder_newton;casadi_rootfinder_nlpsol"  // NOLINT(whitespace/line_length)
#define CASADI_PLUGINS "Linsol::lapacklu;Linsol::lapackqr;Integrator::cvodes;Integrator::idas;Rootfinder::kinsol;Nlpsol::ipopt;Nlpsol::bonmin;Conic::qpoases;Conic::clp;Linsol::csparse;Linsol::csparsecholesky;Linsol::ma27;XmlFile::tinyxml;Nlpsol::blocksqp;Conic::hpmpc;Nlpsol::ampl;Conic::nlpsol;Importer::shell;Integrator::rk;Integrator::collocation;Interpolant::linear;Interpolant::bspline;Linsol::symbolicqr;Linsol::qr;Linsol::ldl;Linsol::lsqr;Nlpsol::sqpmethod;Nlpsol::scpgen;Rootfinder::newton;Rootfinder::nlpsol"  // NOLINT(whitespace/line_length)
#define CASADI_INSTALL_PREFIX "/Users/travis/build/matlab-install"  // NOLINT(whitespace/line_length)

#endif  // CASADI_CONFIG_H // NOLINT(build/header_guard)

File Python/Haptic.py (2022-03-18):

import RPi.GPIO as GPIO  
import time
from icm20948 import ICM20948
import numpy as np
import matplotlib
import matplotlib.pyplot as plt

GPIO.setmode(GPIO.BCM)

imu = ICM20948(0x69)


GPIO.setup(18,  GPIO.OUT)
GPIO.setup(23,  GPIO.OUT)
GPIO.setup(24, 	GPIO.OUT)
GPIO.setup(25, 	GPIO.OUT)

motor1 = GPIO.PWM(18, 48)
motor2 = GPIO.PWM(23, 48)
motor3 = GPIO.PWM(24, 48)
motor4 = GPIO.PWM(25, 48)


motor1.start(5)
motor2.start(5)
motor3.start(5)
motor4.start(5)

time.sleep(5)

for i in range(30):
	motor1.ChangeDutyCycle(4.4 + 0.1*i)
	motor2.ChangeDutyCycle(4.4 + 0.1*i)
	motor3.ChangeDutyCycle(4.4 + 0.1*i)
	motor4.ChangeDutyCycle(4.4 + 0.1*i)
	time.sleep(0.1)


a = 0.8
b = 0.15
c = 0.19
d = 0.03

k = np.array([[		0,	 	-a, 	 b,		0,		-c,		d],
			[		a,		0,		-b,		c,		0,		-d],
			[		0,		 a,	 	b,		0, 		c,		d],
			[		-a,		0,		-b,		-c,		0,		-d]])

R = np.array([	[-0.7071, -0.7071],
				[ 0.7071, -0.7071]])


percent = 0.06
Angle = np.zeros(3)
timesample = 0.015
err = np.zeros(6)
print('start of the controller')

for i in range(3000):

	start = time.time()

	ax, ay, az, gx, gy, gz = imu.read_accelerometer_gyro_data()

	a = np.array([ax, ay])
	a = np.matmul(R,a)

	AccY = -(np.arctan(a[0] / np.sqrt(np.power(a[1], 2) + np.power(az, 2))))
	AccX = (np.arctan(a[1] / np.sqrt(np.power(a[0], 2) + np.power(az, 2))))

	Acc = np.array([AccX, AccY, 0])
	
	gx = (gx - 0.6030)/37.44
	gy = (gy - 0.8427)/37.44
	gz = (gz - 0.1221)/37.44

	gyro = np.array([gx,gy])
	gyro = np.matmul(R,gyro)

	gyro = np.append(gyro, gz)

	Gangles = np.add(Angle, timesample * gyro)

	Angle = np.add(0.96 * Gangles, 0.04 * Acc) #in rad

	err = np.add(err,np.append(Angle,np.zeros(3)))
	state = np.append(Angle, gyro)
	
	t = np.add(-(1-percent)*np.matmul(k, state),- percent * np.matmul(k, err))*1600
	t = np.add(t, np.ones(4)*0.0)

	t[t < 0] = 0

	dc = np.sqrt(t/255) + 4.4

	motor1.ChangeDutyCycle(dc[0])
	motor2.ChangeDutyCycle(dc[1])
	motor3.ChangeDutyCycle(dc[3])
	motor4.ChangeDutyCycle(dc[2])
	
	end = time.time()
	elapsed = end - start
	time.sleep(timesample - elapsed)


motor1.stop()
motor2.stop()
motor3.stop()
motor4.stop()

GPIO.cleanup()

#####

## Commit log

2022-01-08 final update
    [Cellulo concept.f3d, Cellulo concept.stl, Cellulo.stl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]
2022-02-20 add ppt
    [Cellulo.stl, Motorbench Top.step, Motorbench Top.stl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]
